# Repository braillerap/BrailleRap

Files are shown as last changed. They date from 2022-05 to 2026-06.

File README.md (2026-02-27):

<figure>
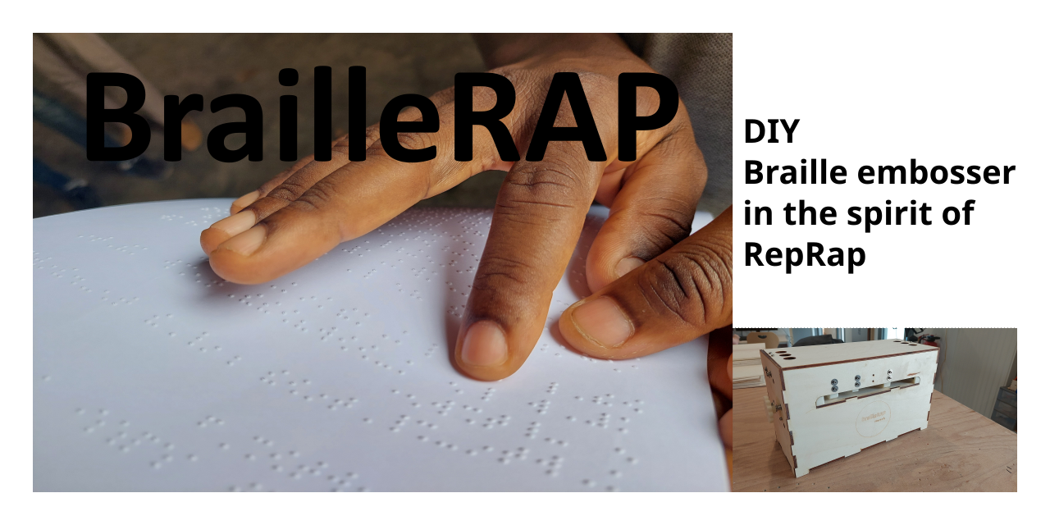
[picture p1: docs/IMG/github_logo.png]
BrailleRAP image

</figure>

# BrailleRAP

## Introduction
Based on a [RepRap 3d printer controller](https://reprap.org/wiki/RepRap), [BrailleRAP](https://github.com/braillerap/BrailleRap) is an open hardware device to emboss Braille text and/or Vector graphics. You can use software like [AccessBrailleRAP](https://github.com/braillerap/AccessBrailleRAP) or [DesktopBrailleRAP](https://github.com/braillerap/DesktopBrailleRAP) to translate text in Braille and build tangible documents with the device. Some tools like [OpenStreetTouch](https://github.com/braillerap/OpenStreetTouch) can help you extract data from [OpenStreetMap](https://www.openstreetmap.org) to build public transport guide or small area city map.

BrailleRAP now exist in 2 different sizes: **BrailleRAP** and **BrailleRAP XL**. 
- **BrailleRAP** emboss sheet up to 210x297 mm. Lightweight, a completed device will weight less than 5 kg and fit in cabin travel case. 
- **BrailleRAP XL** emboss sheet up to 297x420 mm. A larger surface if you need more space to emboss vector graphics. 

<figure>
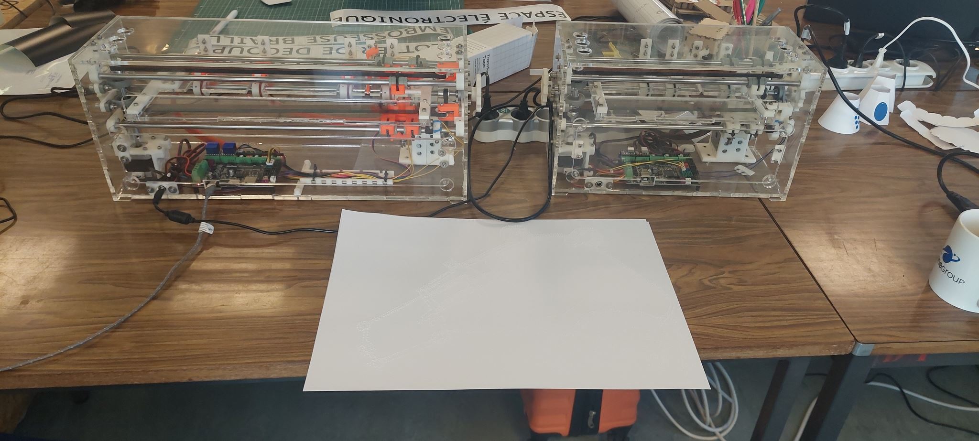
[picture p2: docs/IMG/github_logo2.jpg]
BrailleRAP and BrailleRAP XL image

</figure>

<figure>
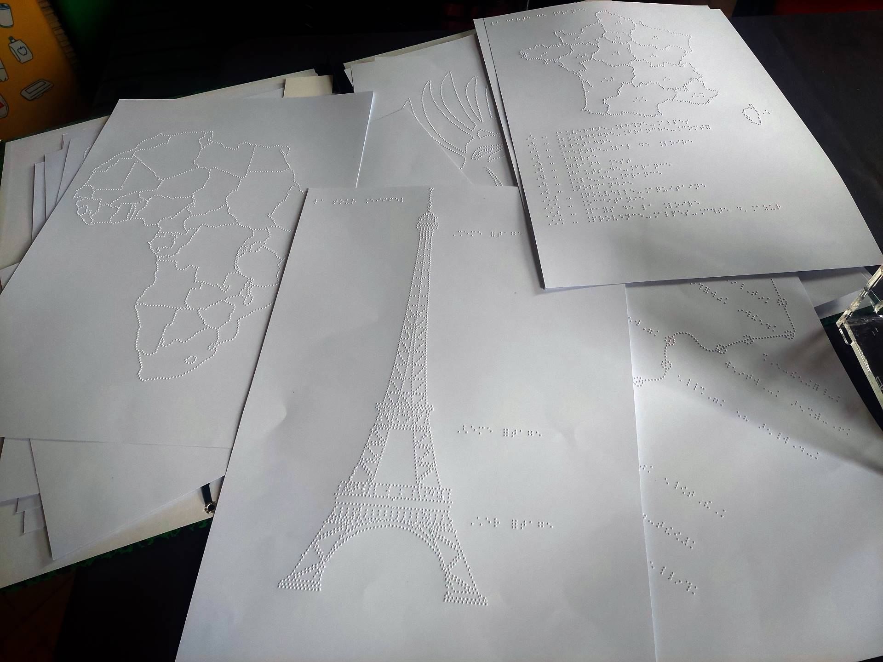
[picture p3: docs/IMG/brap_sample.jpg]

</figure>
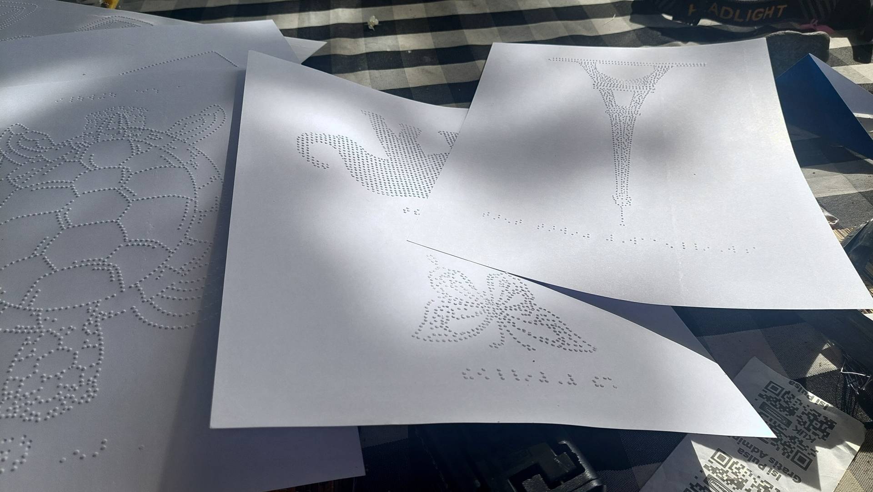
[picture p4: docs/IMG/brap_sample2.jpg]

</figure>

You may also find some interest in some 'side' projects to extend your BrailleRAP usage :

  [OpenStreetTangible](https://github.com/braillerap/OpenStreetTangible), a tangible subway map of the Rennes city in France. A custom build to demonstrate the ability of OpenStreetTouch and BrailleRAP to build accessible map.

  If you built a **BrailleRAP XL** maybe you want to carry it easily. The transport bag for the **BrailleRAP XL** is available [here](https://github.com/braillerap/braillerap-bag). Many thanks to [pasfou](https://github.com/pasfou) for this brilliant idea and realization.

  <figure>
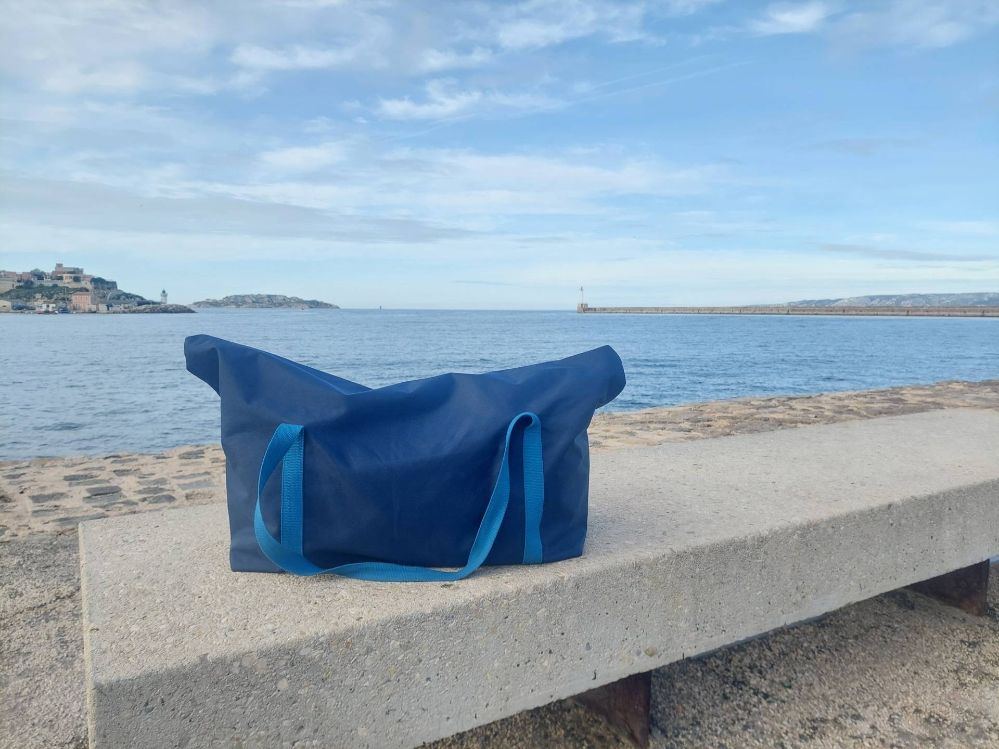
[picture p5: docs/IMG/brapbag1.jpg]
A custom bag for BrailleRAP XL
    
  </figure>

  **En_Bosse** a [Handitechlab Inria](https://project.inria.fr/handitechlabinria/fr/) project to process ultrasound imagery. The project AIM to emboss ultrasound imagery to make it available for visual impaired parents. [Em_Bosse](https://gitlab.inria.fr/handitechlabinria/enbosse/en_bosse/-/blob/main/README.md?ref_type=heads).

  **Carnet_de_sante** a [Handitechlab Inria](https://project.inria.fr/handitechlabinria/fr/) project to make children growing health data available for visual impaired peoples. [Carnet_de_sante](https://gitlab.inria.fr/handitechlabinria/enbosse/carnet_de_sante/-/blob/main/README.md?ref_type=heads).

  **Tactipix** a [Handitechlab Inria](https://project.inria.fr/handitechlabinria/fr/) starting collection of children illustrated books with audio resources (in french). The illustrations can be embossed on BrailleRAP. [Tactipix](https://handitechlabinria.gitlabpages.inria.fr/tactipix/)

## OSHWA Certification

BrailleRAP is [OSHWA](https:oshwa.org) open source hardware certified.
<a href="https://certification.oshwa.org/fr000027.html">
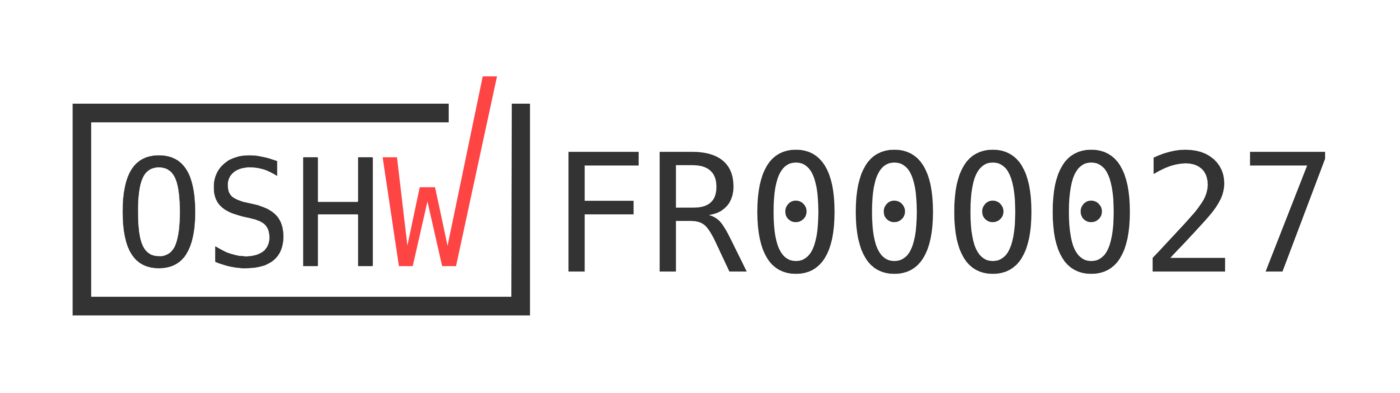
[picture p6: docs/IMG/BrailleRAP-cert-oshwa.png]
OSHWA certificate

</a>

## Building manual
The building manual translation files are available [on codeberg weblate host](https://translate.codeberg.org/projects/braillerap-building-manual/) . If you need the building manual in your language, feel free to contribute on codeberg/weblate.    

<a href="https://translate.codeberg.org/engage/braillerap-building-manual/">
User manual translation status
</a>

## Funding

This project is funded through [NGI0 Entrust](https://nlnet.nl/entrust), a fund established by [NLnet](https://nlnet.nl) with financial support from the European Commission's [Next Generation Internet](https://ngi.eu) program. Learn more at the [NLnet project page](https://nlnet.nl/project/BrailleRAP).

[NLnet foundation logo](https://nlnet.nl)
[NGI Zero Logo](https://nlnet.nl/entrust)

## BrailleRap 6.x Building Manual

Embosseuse Braille Open Source DIY



La documentation complete [est disponible ici braillerap.readthedocs.io](https://braillerap.readthedocs.io/fr/latest/index.html).

==========================================================================

DIY Open Source Braille embosser



The full documentation [is available at braillerap-en.readthedocs.io](https://braillerap-en.readthedocs.io/en/latest/index.html).

## Repository Structure

### `docs/`
The source file for readthedoc documentation, viewable at [braillerap.readthedocs.io](https://braillerap.readthedocs.io/fr/latest/index.html).

### `lasercut/`
SVG/DXF file for laser cut

### `MarlinBraille/`
BrailleRAP Firmware for MKS GEN 1.4 & MKS GEN L 2.1.

The firmware is already configured for DRV8825 stepper drivers.

### `printed_parts/`
STL files for 3D printed parts.

There is an xlsx (3D printed parts excel board.xlsx) files that detail the parts to print.

### `NatBrailleTools/`
Java source code for NatBraille BrailleRAP driver. This is obsolete now. Consider using AccessBrailleRAP (https://github.com/braillerap/AccessBrailleRAP) instead.

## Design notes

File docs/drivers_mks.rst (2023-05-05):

Windows USB Drivers pour MKS 1.4 ou MKS GEN L 2.1
=================================================

Pour MakerBase MKS 1.4
----------------------

Télécharger le driver FTDI (Virtual COM Port Drivers) ici: https://ftdichip.com/drivers/vcp-drivers/

Installer le driver

Pour MakerBase MKS GEN L 2.1
----------------------------

Télécharger le driver CH340 (CH341SER.EXE) ici : https://www.wch.cn/download/CH341SER_ZIP.html

Installer le driver

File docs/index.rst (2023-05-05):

Bienvenue sur la documentation BrailleRAP 
=========================================

.. image :: ./IMG/brailleRAP_couv.jpg 
  :width: 400px
  :align: center

|
 
Contenu:

.. toctree::
   :maxdepth: 1

   history
   licence
   bom
   assemblage
   drivers_mks
   marlin
   firstembossingpage

.. index:: history, licence, bom, marlin, assemblage, firstembossingpage

Mise à jour: |today|

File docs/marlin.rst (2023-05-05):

Marlin Firmware pour cartes Ramps ou compatibles
================================================

.. Note:: Le firmware Marlin est utilisé pour contrôler l'embosseuse Braille. Nous utilisons la configuration CNC pour contrôler l'électro-aimant avec les commandes associées au moteur de CNC / stylo / laser (GCODE M3 et M4)

.. Note:: Le firmware Marlin qui se trouve dans le repertoire MarlinBraille https://github.com/braillerap/BrailleRap/tree/master/MarlinBraille est déja configuré pour la BrailleRAP. Si vous n'avez pas effectué de modifications par rapport à la documentation, vous pouvez l'utiliser directement sans vous préoccuper de la configuration Marlin

Configuration Marlin
--------------------
 
in configuration.h

Motherboard configuration ::

   #ifndef MOTHERBOARD
     //#define MOTHERBOARD BOARD_RAMPS_14_EFB
     #define MOTHERBOARD BOARD_RAMPS_14_SF
   #endif

Spindle / laser / pen configuration ::

   // BRAILLE RAP CONFIG
   #define SPINDLE_LASER_ENABLE
   #define SPINDLE_LASER_ENABLE_PIN  RAMPS_D8_PIN      // !!! for BED MOSFET
   #define SPINDLE_LASER_PWM_PIN     RAMPS_D10_PIN     // !!! for E0 MOSFET
   #define SPINDLE_DIR_PIN           5                 // pin servo

Endstop configuration ::

   // Mechanical endstop with COM to ground and NC to Signal uses "false" here (most common setup).
   #define X_MIN_ENDSTOP_INVERTING false // set to true to invert the logic of the endstop.
   #define Y_MIN_ENDSTOP_INVERTING false // set to true to invert the logic of the endstop.
   #define Z_MIN_ENDSTOP_INVERTING false // set to true to invert the logic of the endstop.
   #define X_MAX_ENDSTOP_INVERTING false // set to true to invert the logic of the endstop.
   #define Y_MAX_ENDSTOP_INVERTING false // set to true to invert the logic of the endstop.
   #define Z_MAX_ENDSTOP_INVERTING false // set to true to invert the logic of the endstop.
   #define Z_MIN_PROBE_ENDSTOP_INVERTING false // set to true to invert the logic of the probe.

Motor step / mm ::

   #define DEFAULT_AXIS_STEPS_PER_UNIT   { 80, 46, 4000, 500 }

Max feedrate ::

   #define DEFAULT_MAX_FEEDRATE          { 300, 300, 5, 25 }

Acceleration ::

   #define DEFAULT_MAX_ACCELERATION      { 1500, 1500, 100, 10000 }

   #define DEFAULT_ACCELERATION          1500    // X, Y, Z and E acceleration for printing moves
   #define DEFAULT_RETRACT_ACCELERATION  1500    // E acceleration for retracts
   #define DEFAULT_TRAVEL_ACCELERATION   1500    // X, Y, Z acceleration for travel (non printing) moves

Jerk ::

   #define DEFAULT_XJERK                 5.0
   #define DEFAULT_YJERK                 5.0
   #define DEFAULT_ZJERK                 0.3
   #define DEFAULT_EJERK                 5.0

.. Note:: Dans la version présente sur le github du projet BrailleRap, d'autres fichiers ont été modifiés pour gérer l'alimentation du papier avec le fin de course de l'axe Y.

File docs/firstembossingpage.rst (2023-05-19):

Embosser votre première page de Braille
=======================================

BrailleRap est une machine qui se pilote en G-CODE, pour embosser du braille il faut tout d'abord traduire le texte en Braille.
Il existe 3 solutions pour traduire le Braille :
L'application AccessBrailleRap https://github.com/braillerap/AccessBrailleRAP/releases
L'application BrailleRap en ligne https://crocsg.github.io/BrailleRap/
L'application NatBraille http://natbraille.free.fr  

Utilisation de l'application AccessBrailleRap
---------------------------------------------
Utiliser le bouton "Paramêtres" pour accéder à l'écran de paramétrage

.. image :: ./IMG/AccBrap-3.png
    :align: center

Choisisser la table Braille de votre choix, le port de communication pour piloter BrailleRAP,
et la langue de l'application

|

Utiliser le bouton "Saisie" pour accéder à l'écran de saisie du texte
Entrer le texte de votre choix, vous pouvez utiliser le copier coller pour 
utiliser un texte existant (page web, document word ...)

.. image :: ./IMG/AccBrap-1.png
    :align: center

|

Utiliser le bouton "Impression" pour accéder à l'écran de d'impression
Sélectionner la page que vous souhaitez embosser avec les boutons "Page précédente" et "Page suivante".
Pour embosser le texte, installer une feuille de papier dans BrailleRAP et utiliser le bouton "Imprimer"

.. image :: ./IMG/AccBrap-2.png
    :align: center

|

Utilisation de l'application BrailleRap
---------------------------------------

Aller sur la page https://crocsg.github.io/BrailleRap/

.. image :: ./IMG/braillerapapp.png 
       :align: center
       
Entrer votre texte à l'endroit indiqué, et télécharger ensuite le fichier GCODE contenant les instructions pour l'embosseuse

.. image :: ./IMG/braillerapapp_download.png
       :align: center

Vous pouvez ensuite utiliser un logiciel comme **cura** ou **pronterface** pour envoyer le fichier GCODE à l'imprimante

Configuration NatBraille
------------------------

Compiler les programmes dans le repertoire NatBrailleTools du projet

Dans les options générales NatBraille, utiliser **TbFr2007** pour la table braille, Encodage document noir **Automtique**, Encodage document braille **Windows1252**

.. image :: ./IMG/natbraille.png
       :align: center

Dans les options d'embossage, utiliser **TbFr2007** pour la table braille pour l'embossage

Activer l'option **utiliser une commande systeme pour l'embossage**

le paramêtre  pour commande d'impression est : **java -jar d:\\usr\\home\\logger\\BrailleLogger.jar $f | java -jar d:\\usr\\home\\logger\\gcodestreamer.jar COM4 250000**
en modifiant eventuellement les repertoires d'installation des programmes
COM4 est le port serie utilisé pour communiquer avec l'imprimante

.. image :: ./IMG/natbrailleembossig.png
       :align: center

Dans les options de mise en page, indiquer 31 et 26 dans le nombre de caracter par ligne et le nombre de lignes par page

.. image :: ./IMG/natbraille_page.png
       :align: center

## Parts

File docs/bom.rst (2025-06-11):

Liste du matériel
=================

Découpe laser
-------------

Pour BrailleRAP
<<<<<<<<<<<<<<<
2 planches de contreplaqué 5mm en 600mm x 400mm.

Les fichiers au format dxf sont disponibles ici : https://github.com/BrailleRap/BrailleRap/tree/master/lasercut
   * lasercut/Braillerap_v6-5-1_600x400-planche1.svg
   * lasercut/Braillerap_v6-5-1-600x400-planche2.svg

Pour BrailleRAP XL
<<<<<<<<<<<<<<<<<<
2 planches de contreplaqué 5mm en 900mm x 400mm.

Les fichiers au format dxf sont disponibles ici : https://github.com/BrailleRap/BrailleRap/tree/master/lasercut
   * lasercut/brapxl-v6.6-planche1_900x400.svg
   * lasercut/brapxl-v6-6-planche2_900x400.svg

Pièces imprimées
----------------
Toutes les pièces sont imprimées en ABS, 50% de remplissage, 3 périmètres extérieurs. Nous utilisons le filament eSun ABS Natural.

Les fichiers au format stl sont ici : https://github.com/braillerap/BrailleRap/tree/master/printed_parts

Pièces mécaniques
-----------------

Pour BrailleRAP
<<<<<<<<<<<<<<<

=== =========================================
Qty Type
=== =========================================
4   Rail de guidage linéaire ( diamètre 8mm ) **330 mm** length
1   Rail de guidage linéaire ( diamètre 8mm ) **365 mm** length
1   Rail de guidage linéaire ( diamètre 8mm ) **100 mm** length

2   630 mm de courroie GT2

3   Joints torique 15.1 mm diamètre intérieur 20.5 mm de diamètre extérieur (15.1 x 20.5 x 2.7)
3   Ressorts tendeurs de courroie GT2

...
=== =========================================

Pour BrailleRAP XL
<<<<<<<<<<<<<<<<<<

=== =========================================
Qty Type
=== =========================================
4   Rail de guidage linéaire ( diamètre 8mm ) **470 mm** length
1   Rail de guidage linéaire ( diamètre 8mm ) **505 mm** length
1   Rail de guidage linéaire ( diamètre 8mm ) **100 mm** length

2   960 mm de courroie GT2

4   Joints torique 15.1 mm diamètre intérieur 20.5 mm de diamètre extérieur (15.1 x 20.5 x 2.7)
4   Ressorts tendeurs de courroie GT2
...
=== =========================================

Pièces communes BrailleRAP XL / BrailleRAP
<<<<<<<<<<<<<<<<<<<<<<<<<<<<<<<<<<<<<<<<<<

=== =========================================
Qty Type
=== =========================================
6   RJ4JP-01-08 palier linéaire Polymer  

3   GT2 poulie 20 dents pour axe 8mm    
2   GT2 poulie libre 20 dents axe 3mm (avec roulement à billes)
1   GT2 poulie 20 dents pour axe 5mm

2   KP08  pallier horizontal pour rail linéaire 8mm 
2   KFL08 pallier vertical pour rail linéaire 8mm 

1   Accouplement d'axe 5mm/8mm

1   Courroie GT2 fermée 200 mm

10	Colliers de serrage 2.5 x 160 mm

...
=== =========================================

Carte controleur
----------------
En fonction de vos souhaits vous pouvez utiliser au choix :

- Une carte MKS GEN 1.4 (Mega2560) et 2 drivers DRV8825 https://github.com/makerbase-mks
- Une carte MKS GEN-L (Mega2560) et 2 drivers DRV8825 https://github.com/makerbase-mks
- Une carte MKS TinyBee (ESP32) et 2 drivers TMC2209 https://github.com/makerbase-mks

D'autres configuration sont possibles, mais vous devrez effectuer la configuration du firmware vous même

Electronique
------------

=== ===========================================================================================
Qty Type
=== ===========================================================================================
2   Moteurs Nema 17 40 N/cm 40mm avec câble (17HS4401).        
1   Electro-aimant *tau-826b* 12V 2A.
1   MKS GEN 1.4 ou carte compatible Ramps 1.4 ou MKS GEN L 2.1 https://github.com/makerbase-mks.
2   drivers DRV8825 avec radiateur.
1   1N4004  diode de roue libre ou equivalent (12V 2A) (pour MKS GEN 1.4 uniquement).    
2   Commutateurs fin de course cablés conformément à la documentation. (OMRON `SS-5GL <https://omronfs.omron.com/en_US/ecb/products/pdf/en-ss.pdf>`_ ou compatible)
1   Embase Alimentation jack 2.5mm. 
1   Alimentation 12v 6A jack 2.5mm.

=== ===========================================================================================

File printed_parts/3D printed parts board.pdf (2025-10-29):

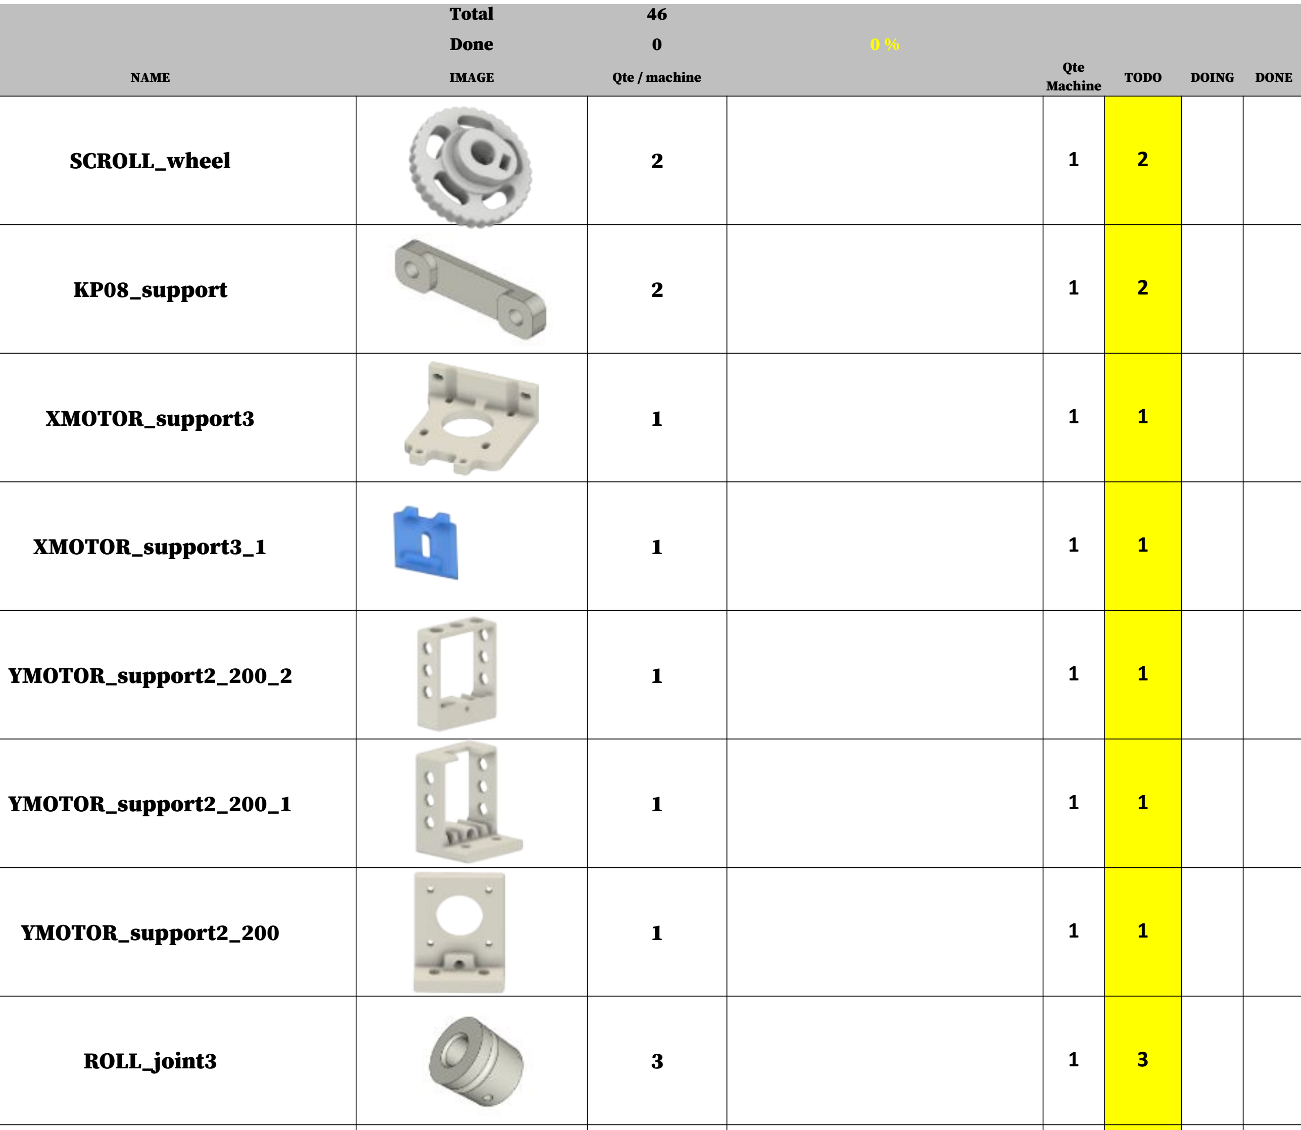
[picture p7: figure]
Total; Done; NAME; IMAGE; Qte / machine; TODO; DOING DONE; SCROLL_wheel; KP08_support; XMOTOR_support3; XMOTOR_support3_1; YMOTOR_support2_200_2; YMOTOR_support2_200_1; YMOTOR_support2_200; ROLL_joint3; Qte Machine
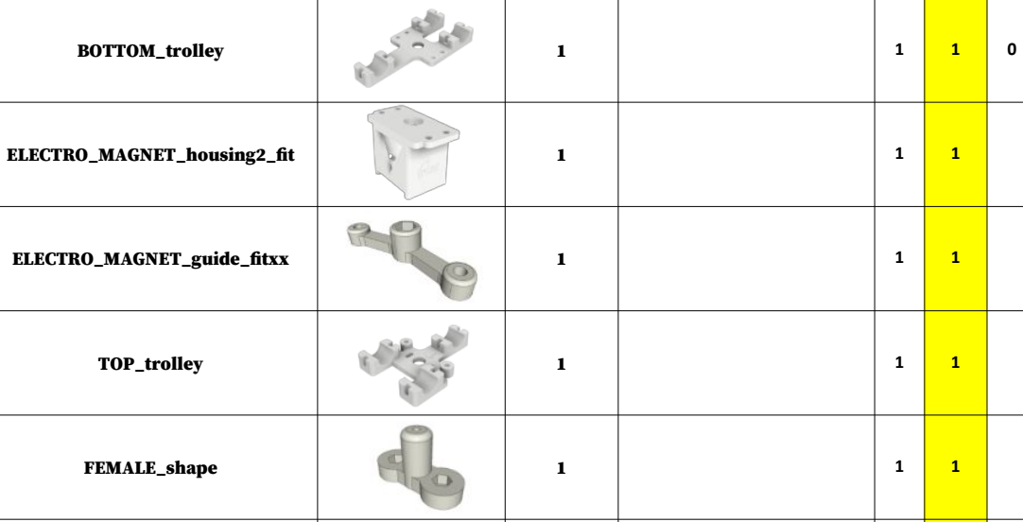
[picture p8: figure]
BOTTOM_trolley; ELECTRO_MAGNET_housing2_fit; ELECTRO_MAGNET_guide_fitxx; TOP_trolley; FEMALE_shape

LID_LOCK | 2 | 1 | 2
BOTTOM_AXIS_left2 | 1 | 1 | 1

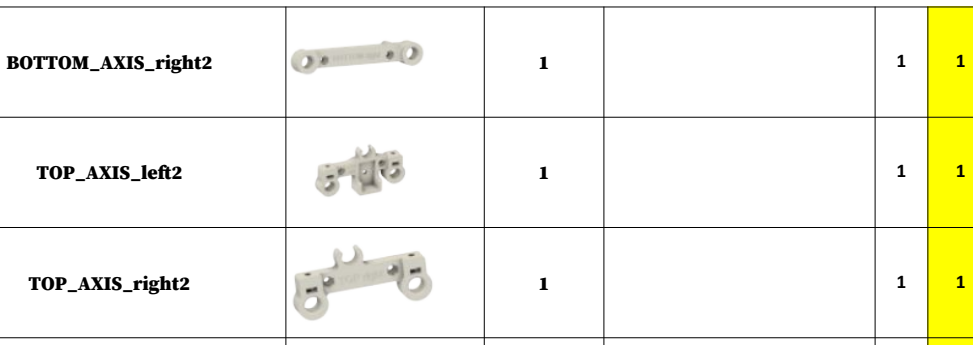
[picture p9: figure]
BOTTOM_AXIS_right2; TOP_AXIS_left2; TOP_AXIS_right2

DRIVEN_PULLEY_housing | 2 | 1 | 2
PAPER_GUIDE_left (A4) or paper_guide_left (XL) | 1 | 1 | 1
PAPER_GUIDE_right (A4) or paper_guide_right (XL) | 1 | 1 | 1
ENDSTOP_Y_support | 1 | 1 | 1
ENDSTOP_Y_lever_weight2 | 1 | 1 | 1
ENDSTOP_X_support | 1 | 1 | 1
CLIPBOARD_2 | 4 | 1 | 4
CLIPBOARD_2_SUPPORT | 4 | 1 | 4

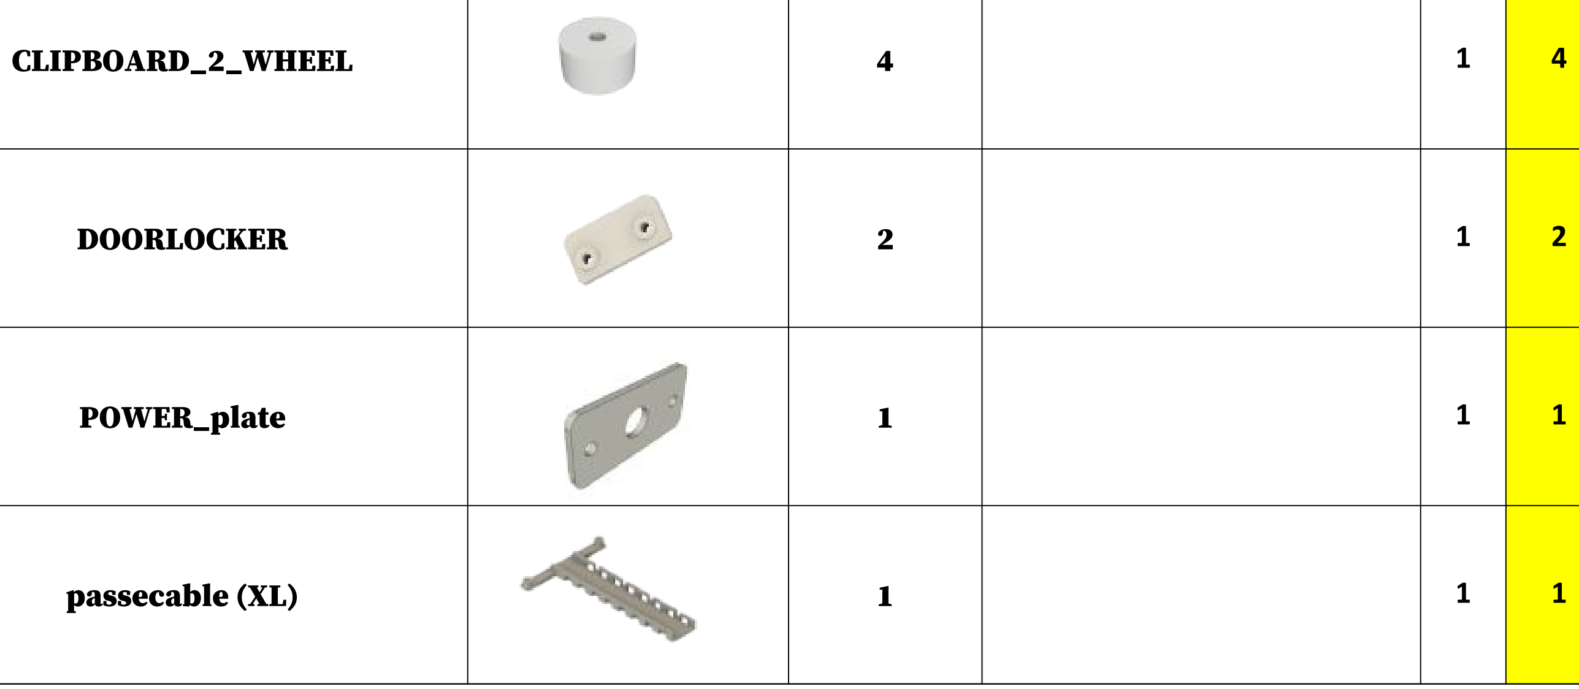
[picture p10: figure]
CLIPBOARD_2_WHEEL; DOORLOCKER; POWER_plate; passecable (XL)

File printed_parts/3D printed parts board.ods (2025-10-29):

 | Total | 46
 | Done | 0 | 0 %
NAME | IMAGE | Qte / machine |  | Qte Machine | TODO | DOING | DONE
SCROLL_wheel |  | 2 |  | 1 | 2
KP08_support | Capture d’écran 2018-04-30 à 12.50.34.png | 2 |  | 1 | 2
XMOTOR_support3 |  | 1 |  | 1 | 1
XMOTOR_support3_1 |  | 1 |  | 1 | 1
YMOTOR_support2_200_2 |  | 1 |  | 1 | 1
YMOTOR_support2_200_1 |  | 1 |  | 1 | 1
YMOTOR_support2_200 |  | 1 |  | 1 | 1
ROLL_joint3 | Capture d’écran 2018-04-23 à 12.45.35.png | 3 |  | 1 | 3
BOTTOM_trolley |  | 1 |  | 1 | 1 | 0
ELECTRO_MAGNET_housing2_fit |  | 1 |  | 1 | 1
ELECTRO_MAGNET_guide_fitxx | Capture d’écran 2018-04-30 à 13.00.29.png | 1 |  | 1 | 1
TOP_trolley |  | 1 |  | 1 | 1
FEMALE_shape | Capture d’écran 2018-04-23 à 13.38.51.png | 1 |  | 1 | 1
LID_LOCK | Capture d’écran 2018-04-23 à 13.41.41.png | 2 |  | 1 | 2
BOTTOM_AXIS_left2 |  | 1 |  | 1 | 1
BOTTOM_AXIS_right2 |  | 1 |  | 1 | 1
TOP_AXIS_left2 |  | 1 |  | 1 | 1
TOP_AXIS_right2 |  | 1 |  | 1 | 1
DRIVEN_PULLEY_housing | Capture d’écran 2018-04-26 à 10.52.19.png | 2 |  | 1 | 2
PAPER_GUIDE_left (A4) or paper_guide_left (XL) |  | 1 |  | 1 | 1
PAPER_GUIDE_right (A4) or paper_guide_right (XL) |  | 1 |  | 1 | 1
ENDSTOP_Y_support |  | 1 |  | 1 | 1
ENDSTOP_Y_lever_weight2 |  | 1 |  | 1 | 1
ENDSTOP_X_support |  | 1 |  | 1 | 1
CLIPBOARD_2 |  | 4 |  | 1 | 4
CLIPBOARD_2_SUPPORT |  | 4 |  | 1 | 4
CLIPBOARD_2_WHEEL |  | 4 |  | 1 | 4
DOORLOCKER |  | 2 |  | 1 | 2
POWER_plate | Capture d’écran 2018-06-03 à 10.23.29.png | 1 |  | 1 | 1
passecable (XL) |  | 1 |  | 1 | 1

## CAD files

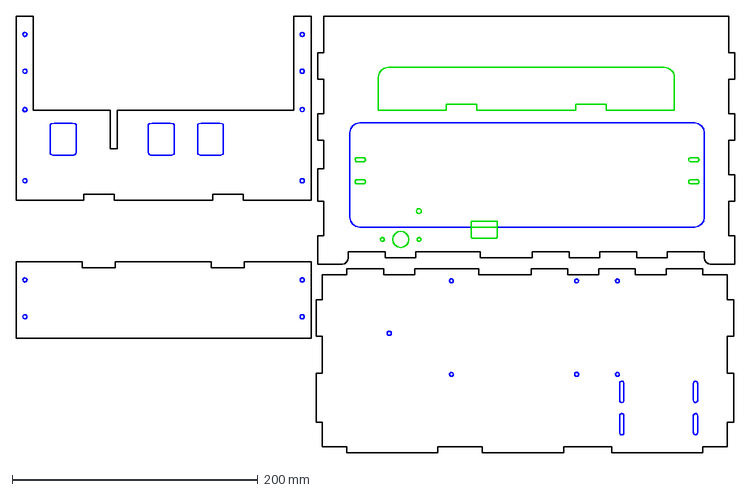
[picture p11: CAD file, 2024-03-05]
lasercut/Braillerap_v6-5-1-600x400-planche2.dxf
585.6 x 355.9 mm

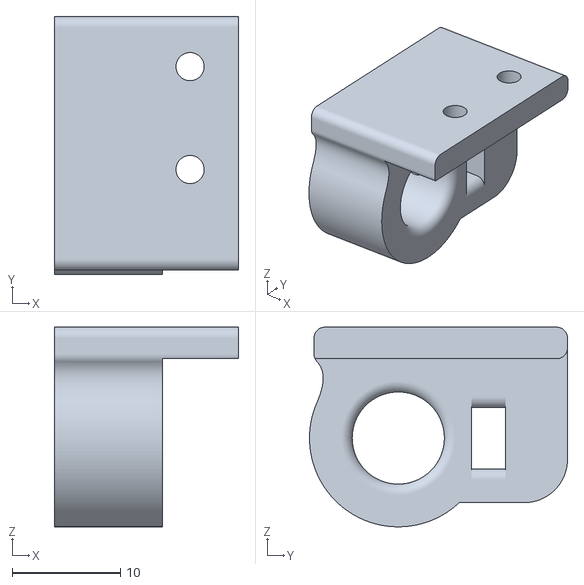
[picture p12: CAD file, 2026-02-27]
printed_parts/ENDSTOPX_support2.stl
17.0 x 23.8 x 18.4

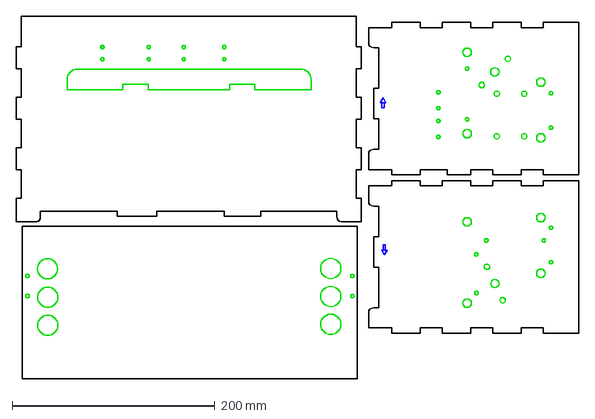
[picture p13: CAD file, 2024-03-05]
lasercut/Braillerap_v6-5-1_600x400-planche1.dxf
553.9 x 356.7 mm

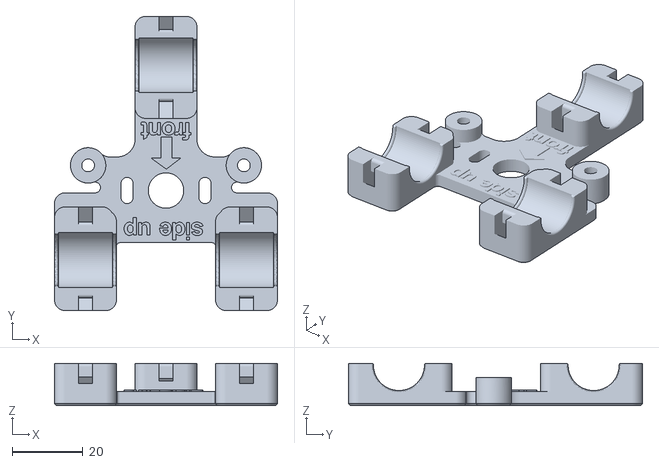
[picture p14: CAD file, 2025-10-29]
printed_parts/TOP_trolley.stl
63.0 x 83.1 x 12.0

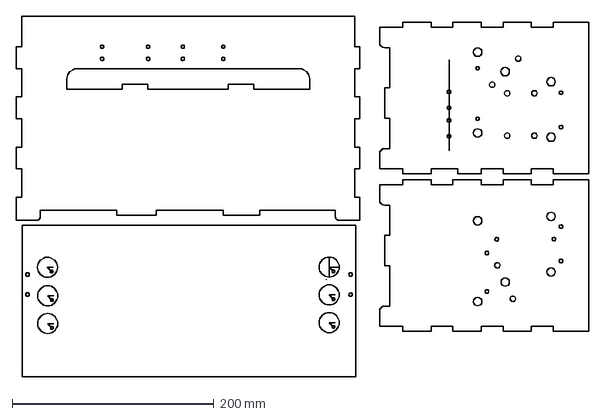
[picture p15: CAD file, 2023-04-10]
lasercut/BrailleRAP V6-5 600x400 planche1.dxf
566.6 x 356.7 mm

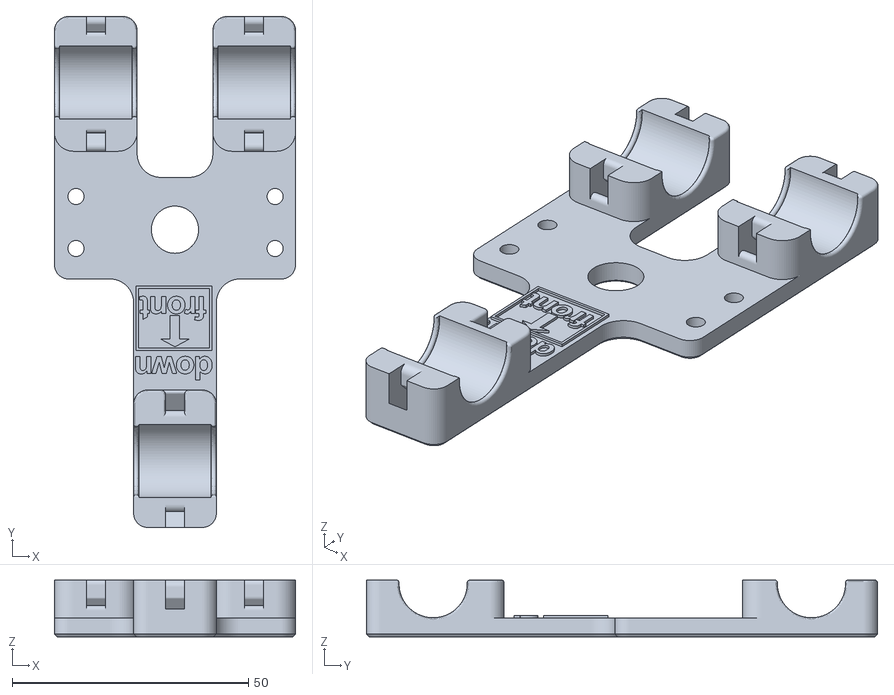
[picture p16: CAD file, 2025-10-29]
printed_parts/BOTTOM_trolley.stl
51.0 x 108.1 x 12.0

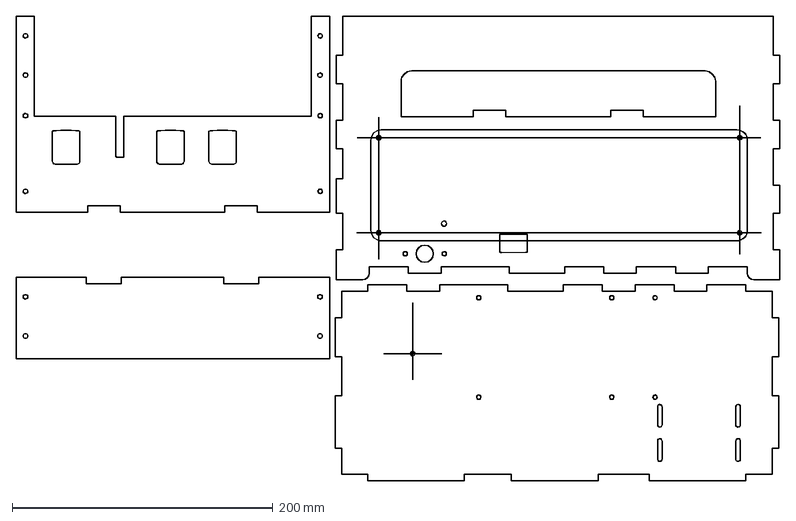
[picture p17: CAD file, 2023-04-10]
lasercut/BrailleRAP V6-5 600x400 planche2.dxf
585.6 x 355.9 mm

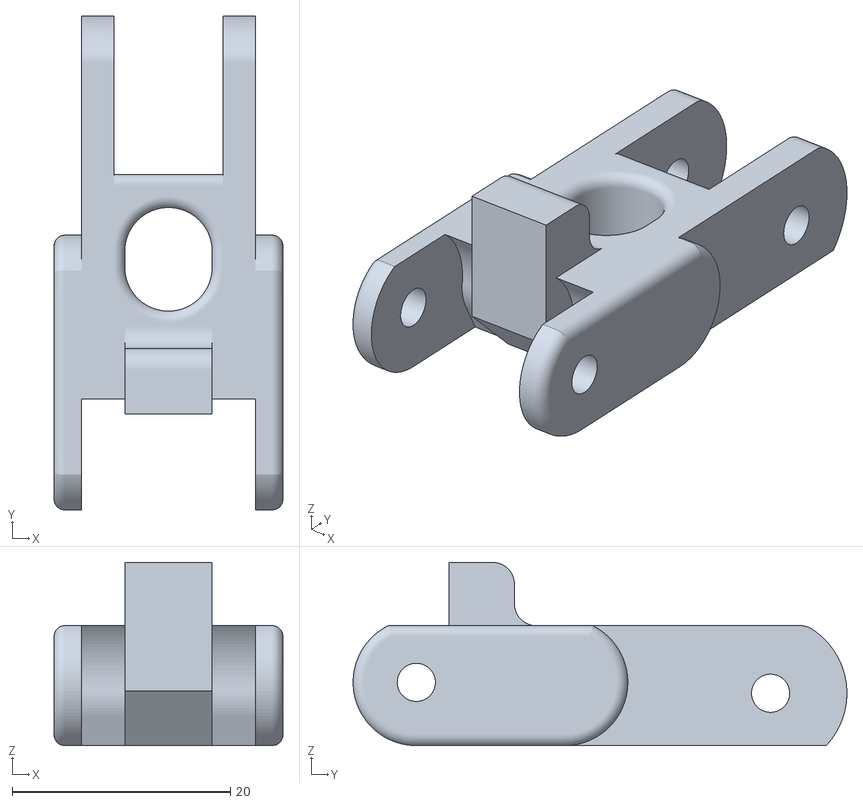
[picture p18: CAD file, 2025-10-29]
printed_parts/clipboard2.stl
21.0 x 45.3 x 16.8

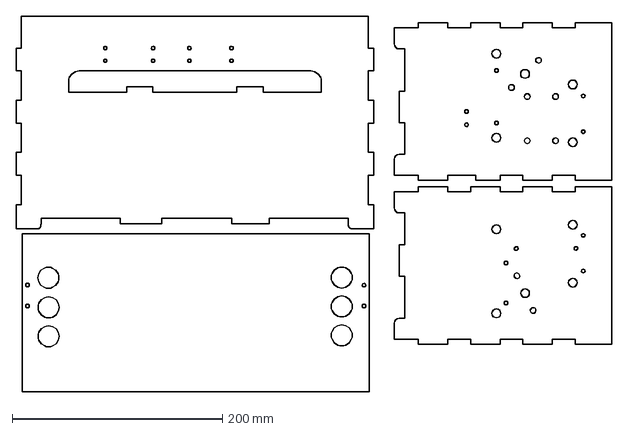
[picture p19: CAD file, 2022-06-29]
lasercut/BrailleRAP V6 600x400 planche1.dxf
566.6 x 356.7 mm

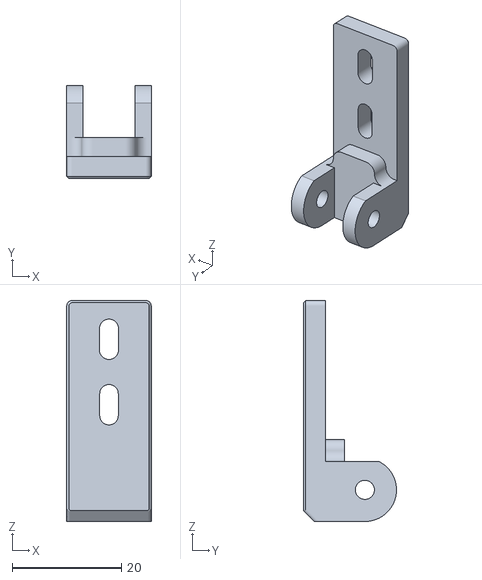
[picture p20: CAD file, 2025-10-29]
printed_parts/clipboard2_support.stl
15.5 x 17.0 x 40.5

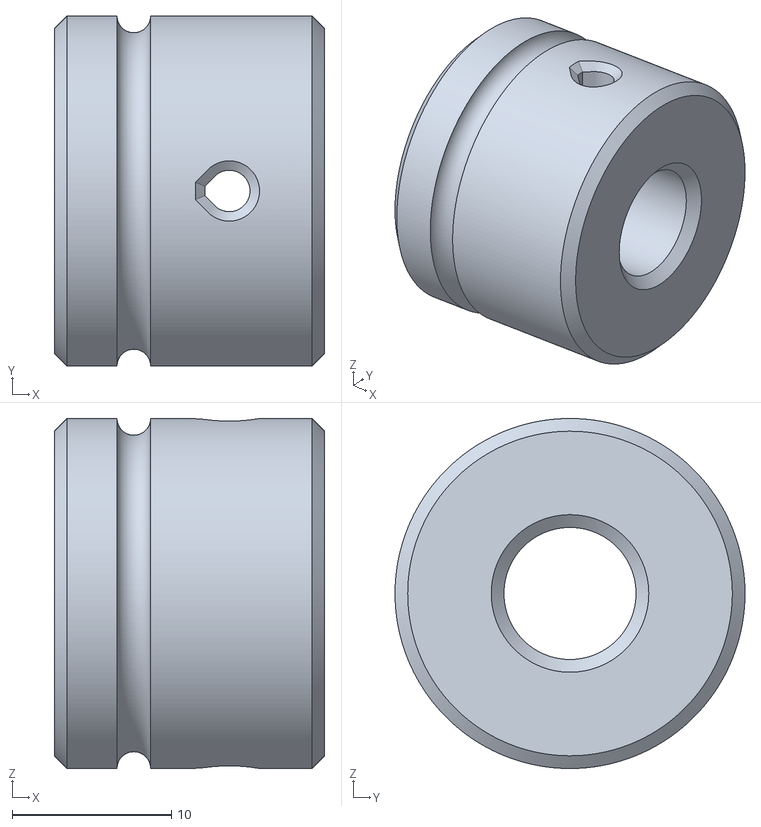
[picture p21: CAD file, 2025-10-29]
printed_parts/ROLL_JOINT3.stl
17.0 x 22.0 x 22.0

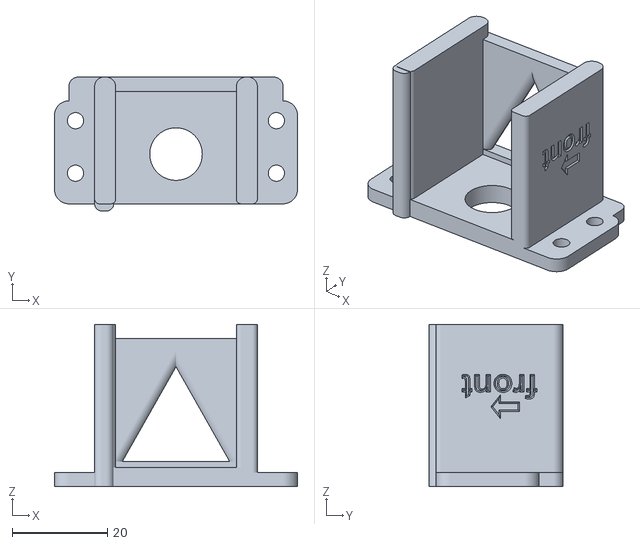
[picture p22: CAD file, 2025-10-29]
printed_parts/ELECTRO_MAGNET_housing_fit.stl
50.9 x 28.1 x 34.0

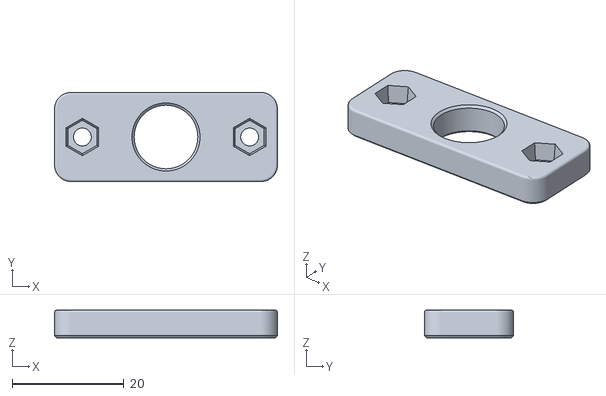
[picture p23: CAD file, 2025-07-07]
printed_parts/power_plate_10mm.stl
40.0 x 16.0 x 5.00

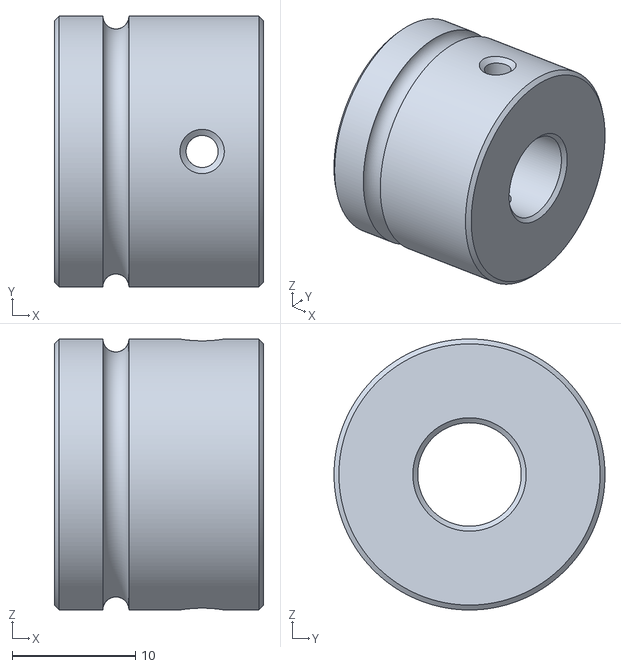
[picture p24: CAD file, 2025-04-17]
printed_parts/ROLL_JOINT2_test.stl
17.0 x 22.0 x 22.0

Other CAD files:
printed_parts/ROLL_JOINT2.stl
printed_parts/YMOTOR_support2_200.stl
printed_parts/YMOTOR_support2_200_1.stl
printed_parts/ELECTRO_MAGNET_housing2.stl
lasercut/BrailleRAP V5 600x400 planche1.dxf
lasercut/OLD/BrailleRAP V5 600x400 planche1.dxf
lasercut/OLD/BrailleRAP V5 600x400 planche2.dxf
lasercut/OLD/BrailleRAP V6 600x400 planche2.dxf
printed_parts/BOTTOM_AXIS_right2.stl
printed_parts/CLIPBOARD2_WHEEL.stl
printed_parts/CLIPBOARD_WHEEL.stl
printed_parts/DOORLOCKER.stl
printed_parts/DRIVEN_PULLEY_housing.stl
printed_parts/ELECTRO_MAGNET_guide.stl
printed_parts/ELECTRO_MAGNET_guide_fit.stl
printed_parts/ELECTRO_MAGNET_guide_fit_5.7.stl
printed_parts/ELECTRO_MAGNET_guide_fit_5.8.stl
printed_parts/ELECTRO_MAGNET_guide_fit_5.9.stl
printed_parts/ELECTRO_MAGNET_guide_fit_6.0.stl
printed_parts/ENDSTOPX_support.stl
printed_parts/ENDSTOP_Y_lever_weight.stl
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

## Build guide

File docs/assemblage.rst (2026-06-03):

Manuel de montage BrailleRAP
============================

Outillages necessaires
----------------------

       - Petites pinces.
       - Petite pince coupante.
       - Un taraud M3.
       - 1 foret de 8mm.
       - 1 foret de 3mm.
       - Clés 6 pans 1.5, 2, 2.5 et 4. 
       - Clés à tube 5.5 et 8.
       - Colle à bois. 
       - Scotch de peintre.

Remarques sur les vis
---------------------

M3 et M5 correspondent au diamètre en mm de la partie taraudée des vis
Le deuxieme nombre correspond à la longueur de la vis
Par exemple M3-12 designe une vis de 3mm de diamètre et de 12mm de longueur

**M5-18** correspond à une vis avec une tête hexagonale (5mm de diamètre 18mm de longueur)
	
	.. image :: ./IMG/vis6pans.jpg
		:align: center

|

**M3-12 sans tête** correspond a une vis sans tête (3mm de diamètre - 12 mm de longueur)

	.. image :: ./IMG/vissantete.jpg
		:align: center

|

Remarques sur les écrous
------------------------

**Ecrou M3 ou ecrou M5** désignent des ecrous standards de diamêtre 3mm ou 5mm

	.. image :: ./IMG/ecrou.jpg
		:align: center

|

**Ecrou M3 NYL** ou **ecrou M5 NYL** désignent des ecrous **frein** de diamêtre 3mm ou 5mm
	
	.. image :: ./IMG/ecrounyl.jpg
		:align: center

|

Remarques BrailleRAP / BrailleRAP XL
------------------------------------

Il existe désormais 2 modèles de BrailleRAP: **BrailleRAP** et **BrailleRAP XL**.

**BrailleRAP** est la version historique de la machine et peut utiliser des feuilles jusqu'au format **A4**.
       
       * Braillerap_v6-5-1_600x400-planche1.svg
       * Braillerap_v6-5-1_600x400-planche2.svg

**BrailleRAP XL** est la version agrandie et peut utiliser des feuilles jusqu'au format **A3**.
       
       * brapxl-v6-6-planche1_900x400.svg
       * brapxl-v6-6-planche2_900x400.svg

Le montage des 2 modèles est très semblable, les principales différences sont :

    * Le montage du plateau papier.
    * Le nombre de rouleaux presse papier.
    * les longeurs de barres lineaires et les longueurs de courroie.
    * BrailleRAP XL demande tout de même un peu plus de rigueur dans l'assemblage mécanique.

|

Collage de la caisse en bois
----------------------------
Matériel:

    * FACE (contre-plaqué de 5mm découpé au laser).
    * BACK (contre-plaqué de 5mm découpé au laser).
    * BOTTOM (contre-plaqué de 5mm découpé au laser).
    * LEFT_SIDE (contre-plaqué de 5mm découpé au laser).
    * RIGHT_SIDE (contre-plaqué de 5mm découpé au laser).
    * Colle à bois.
    * Scotch de peintre.

* Préparer les 5 éléments: FACE, BACK, LEFT_SIDE, RIGHT_SIDE et BOTTOM.

.. ATTENTION:: bien repérer la position des cotés (droit et gauche) et le fond. Utiliser les percages pour orienter les pièces comme sur la figure

.. image :: ./IMG/gluing_chassis.png
       :align: center

|

* Encoller les encoches, assembler les 5 parties et les maintenir en place avec du scotch de peintre le temps du séchage préconisé par le fabricant.

.. image :: ./IMG/BrailleRAP-V5.01.jpg
       :align: center

|

Collage des bloqueurs de trappe
-------------------------------
Matériel:

    * Chassis assemblée.
    * 4 disques en bois récupérés de la découpe laser du couvercle.
    * Colle à bois.

* Coller les 4 disques de bois sur la façade arrière à l'intérieur de la caisse. Ces disques maintiendront la trappe d'accès à l'intérieur de la machine.

.. image :: ./IMG/chassis_disc.png
       :align: center

|

Collage du plateau papier
-------------------------------
Matériel:
	* Support papier supérieur.
	* Support papier inférieur.
	* Colle à bois.
	* Pinces de serrage.
	
.. image :: ./IMG/paper_support_parts.jpg
       :align: center

|

* Coller le support inférieur sous le support supérieur. 

.. image :: ./IMG/paper_support_v8.png
       :align: center

|

.. ATTENTION:: les 2 pièces doivent êtrent parfaitement alignées. Placer des vis dans les percages pour bien aligner les pièces. Il ne doit pas y avoir d'espace entre les deux pièces (ou la feuille de papier pourrait venir se coincer). Bien serrer les pièces l'une contre l'autre avec des pinces de serrages 

Préparation du pointeau Braille
-------------------------------

Matériel :

    * 1 Pierre à aiguisé
    * 1 vis sans tête M3-16 bout téton

* Limer l'arête du téton afin d’obtenir un profil approchant celui illustré.

.. image :: ./IMG/BrailleRAP-V5.56.jpg
       :align: center

|

Préparation Moteur X
--------------------
Matériel :

    * **Pièce(s) imprimée(s) en 3D** :  XMOTOR_support3 ou XMOTOR_support3_1 
    * 1 moteur Nema 17
    * 4 vis M3-8 
    * 2 écrous NYL M3
    * 2 vis M3-14
    
* Insérer 2 écrous NYL M3 dans la piece imprimée **XMOTOR_support3_1**.

.. image :: ./IMG/xmotor_support_assembly_v2_1.png
       :align: center

|

* Fixer les deux pièces imprimée **XMOTOR_support3_1** et **XMOTOR_support3** avec deux vis M3-14.

.. image :: ./IMG/xmotor_support_assembly_v1_2.png
       :align: center

|

* Fixer le moteur dans son support avec 4 vis M3-8. Ne pas serrer les vis, le moteur doit conserver un peu de jeu, il sera fixé ultérieurement.

.. image :: ./IMG/xmotor_support_assembly_v1_3.png
       :align: center

|

.. NOTE:: Attention à l'orientation du connecteur du moteur !

Préparation Moteur Y
--------------------

Matériel :

    * **Pièce(s) imprimée(s) en 3D** :  YMOTOR_support2_200_1, YMOTOR_support2_200_2, YMOTOR_support2_200
    * 1 moteur Nema 17
    * 1 poulie GT2 20 dents bore 5mm
    * 4 vis M3-8 
    * 2 vis M3-12

* Serrer la poulie sur l’arbre du moteur en s’assurant qu’au moins une des deux vis soit en face du méplat de l’axe du moteur et que les dents de la poulie soient orientées vers le moteur.

.. image :: ./IMG/BrailleRAP-V5.03.jpg
       :align: center

|

* Tarauder les deux cotés de la pièce centrale du support (**YMOTOR_support2_200_2**)

.. image :: ./IMG/ymotor_support_assembly_1.png
       :align: center
.. image :: ./IMG/ymotor_support_assembly_2.png
       :align: center

|

* Fixer les pieces **YMOTOR_support2_200_2** et **YMOTOR_support2_200_1** avec une Vis M3-12.

.. image :: ./IMG/ymotor_support_assembly3.png
       :align: center

|

* Fixer la piece **YMOTOR_support2_200** sur l'ensemble précédent avec une vis M3-12.

.. image :: ./IMG/ymotor_support_assembly_4.png
       :align: center

|

* Monter le moteur sur son support avec les 4 vis M3-8 en s'assurant que le connecteur du moteur soit dans la position correspondante à l'illustration.

.. image :: ./IMG/ymotor_support_assembly_5.png
       :align: center

|

* Introduire les écrous 4 NYL M3 dans le support moteur. Les maintenir en place avec un petit bout de scotch de peintre.

.. image :: ./IMG/ymotor_support_assembly_6.png
       :align: center

|

Préparation des supports d’axes
--------------------------------

  * **Pièce(s) imprimée(s) en 3D** : BOTTOM_AXIS_left2
  * **Pièce(s) imprimée(s) en 3D** : TOP_AXIS_left2
  * **Pièce(s) imprimée(s) en 3D** : TOP_AXIS_right2
  * 1 foret de 8mm
  * 6 écrous M3
  * 6 vis M3-12 sans tête

.. ATTENTION:: Selon la qualité d’impression des pièces en plastique, veiller à ce que les barres de 8mm puissent coulisser facilement dans leurs logements. Le cas échéant, percer le trou avec un foret de 8.

* Les 3 pièces à assembler sont les suivantes 

.. image :: ./IMG/Axis_assembly_v1.png
       :align: center

|

* Pour chacune des 3 pièces, introduire un écrou M3 dans les trous rectangulaires. Visser les vis M3-12.

.. image :: ./IMG/BrailleRAP-V5.09.1.jpg
       :align: center

|

* L’extrémité de la vis ne doit pas dépasser dans le passage des barres de Ø 8mm.

.. image :: ./IMG/BrailleRAP-V5.10.jpg
       :align: center

|

.. image :: ./IMG/BrailleRAP-V5.11.jpg
       :align: center

|

Préparation de l'interrupteur de fin de course X
------------------------------------------------

Matériel :

  * **Pièce(s) imprimée(s) en 3D** : SWITCH_X_support
  * 1 interrupteur fin de course câblé (cf câblage des interrupteurs fin de course)
  * 1 vis sans tête M3-12
  * 1 écrou M3
  * 2 vis M2.5-14
  * 2 écrous M2.5 NYL

* Introduire un écrou M3 et visser une vis sans tête M3-12.

.. image :: ./IMG/BrailleRAP-V5.45.png
       :align: center
.. image :: ./IMG/BrailleRAP-V5.45-1.png
       :align: center

|

* Visser l'interrupteur fin de course sur son support (ENDSTOP_X_support) à l'aide des vis M2.5-14 et des écrous M2.5.

.. Note:: L'interrupteur fin de course devra être câblé avant le montage.
.. Note:: Attention au sens des vis 2.5. La tête de la vis doit être sous le microswitch pour permettre le passage de l'axe linéaire.

.. image :: ./IMG/endtsopx_assembly.png
       :align: center

.. Note:: On utilisera de préférence un microswitch cablé dans l'alignement.

.. image :: ./IMG/endstop_droit.jpg
       :align: center

|

Préparation de l’électro-aimant
--------------------------------

Matériel :

  * 1 électro-aimant
  * 1 entretoise de 18mm
  * 1 vis sans tête M3-16 pointeau limée (cf Préparation du pointeau mâle)
  * 1 écrou M3
  * 1 rondelle M3 

* Visser l’entretoise à fond sur l’électro-aimant.

.. image :: ./IMG/BrailleRAP-V5.16.png
       :align: center

|

* Visser la vis M3-16 pointeau limée en la laissant dépasser de ± 6mm de l’entretoise.

.. image :: ./IMG/BrailleRAP-V5.17.png
       :align: center

|

Montage de l'electro-aimant sur son support
-------------------------------------------

Matériel :
  * Ensemble électro-aimant pré assemblé (cf Préparation de l électro-aimant)
  * **Pièce(s) imprimée(s) en 3D ** : ELECTRO_MAGNET_housing2 ou ELECTRO_MAGNET_Housing2_fit
  * 2 vis M3-8
  * 2 rondelles M3

* Sélectionner la pièce **ELECTRO_MAGNET_housing2** ou **ELECTRO_MAGNET_Housing2_fit**. Sur une imprimante 3D d'ancienne génération, on utilisera plutot **ELECTRO_MAGNET_housing2**. Sur une imprimante récente et ultra précise, on utilisera plutôt **ELECTRO_MAGNET_Housing2_fit**. Ce sont les même pièces, mais les tolérances mécaniques sont plus faible sur la version **fit**, ce qui permet un meilleur centrage de l'electro-aimant.

* Fixer l’électro-aimant sur son support avec les 2 vis M3-8 et 2 rondelles M3.

.. ATTENTION:: Respecter le côté de sortie des fils c'est important.

.. image :: ./IMG/BrailleRAP-V5.19.png
       :align: center

|

.. NOTE:: Veuiller à aligner soigneusement le bord du support et le bord de l'electro-aimant

.. image :: ./IMG/BrailleRAP-V5.19-1.png
       :align: center

|

Préparation du chariot bas (étape 1)
------------------------------------

Matériel :

  * Electro-aimant assemblé dans son support
  * **Pièce(s) imprimée(s) en 3D** : BOTTOM_trolley
  * **Pièce(s) imprimée(s) en 3D** : ELECTRO_MAGNET_guide_fitxxx
  * 3 paliers lineaires IGUS
  * 3 colliers de serrage 2.5 x 160
  * 4 écrous M3 NYL
  * 2 vis M3-16
  * 2 vis M3-20

.. NOTE:: Sélectionner la meilleure pièce ELECTRO_MAGNET_guide_fit_5.8 / ELECTRO_MAGNET_guide_fit_5.9 / ELECTRO_MAGNET_guide_fit_6.0. l'entretoise de l'éléctroaimant doit circuler librement avec le minimum de jeu mécanique.

* Introduire les 3 IGUS sur le support BOTTOM_trolley. Les fixer avec des colliers de serrage

.. ATTENTION:: Bloquer les IGUS dans le rainurage. Ne pas serrer les colliers trop fort, ils seront ajustés quand le chariot sera en place sur les rails linéaires

.. image :: ./IMG/bottom_trolley_ok_v9.png
       :align: center

.. image :: ./IMG/bottom_trolley_assembly_v1-1.png
       :align: center

|

.. ATTENTION:: Respecter la position du collier. Le verrouillage du collier doit être du coté de l'IGUS et vers la paroi de la machine.

.. image :: ./IMG/bottom_trolley_assembly-v4.png
       :align: center

|

* Assembler l'électro-aimant (préalablement monté dans son logement) sous le BOTTOM_trolley et le ELECTRO_MAGNET_guide avec les deux vis M3-16 et 2 écrous M3 NYL.

.. ATTENTION:: Selon la qualité de l'impression, il sera peut-être nécessaire de limer le logement de l'entretoise. Notez également que le corps de l'electro-aimant doit être le plus perpendiculaire possible à la plaque support (l'axe doit être au milieu du percage qui permet son pasage). 

.. ATTENTION:: Notez que les fils de l'electro-aimant doivent sortir du coté ou il y a un seul pallier IGUS.

.. image :: ./IMG/BrailleRAP-V5.14-3.png
       :align: center

|

* Visser les deux vis M3-20 (qui retiendront la courroie) et 2 écrous M3 NYL avec la tête de vis en dessous.

.. image :: ./IMG/BrailleRAP-V5.14-4.png
       :align: center

|

* Mettre une rondelle et serrer le contre écrou M3 en veillant à ce que la vis pointeau ne se visse pas en même temps dans l’entretoise. La rondelle empêche le contre écrou de se coincer dans le guide de l’entretoise.

.. image :: ./IMG/BrailleRAP-V5.14-5.png
       :align: center

.. image :: ./IMG/BrailleRAP-V5.18.png
       :align: center

|

.. NOTE:: L'axe de l'electroaimant doit pouvoir monter et descendre librement sans effort.

|

Preparation du chariot haut (étape 1)
-------------------------------------

Matériel :

  * **Pièce(s) imprimée(s) en 3D** : TOP_trolley
  * **Pièce(s) imprimée(s) en 3D** : FEMALE_shape
  * Taraud M3
  * 1 vis sans tête M3-30
  * 1 écrou borgne M3
  * 1 écrou M3
  * 2 vis M3-12
  * 2 rondelles M3
  * 2 vis M3-20
  * 4 écrous M3 NYL
  * 3 paliers lineaires IGUS
  * 3 colliers de serrage 2.5 x 160

* Encoller le pas de vis de l'écrou borgne et visser la vis M3-30 sans tête du côté **SANS** empreinte allen.

.. image :: ./IMG/BrailleRAP-V5.79.jpg
       :align: center

|

* Placer un contre écrou contre l'écrou borgne

* Tarauder la FEMALE_shape au 2/3 en partant du haut.

.. image :: ./IMG/BrailleRAP-V5.80.jpg
       :align: center

|

* Visser l’ensemble vis M3-30/écrou borgne pour le laisser dépasser ± 0,5mm.

.. image :: ./IMG/BrailleRAP-V5.81.jpg
       :align: center

|

* Assembler la FEMALE_shape sur le TOP_trolley avec les vis M3-12, les rondelles M3 et les écrous M3 NYL en laissant du jeu.

.. image :: ./IMG/BrailleRAP-V5.82.png
       :align: center

.. image :: ./IMG/BrailleRAP-V5.83.png
       :align: center

|

* Positionner les paliers IGUS sur la piece TOP_trolley.

.. image :: ./IMG/toptroley_assembly_empty_v3.png
       :align: center

.. image :: ./IMG/toptroley_assembly_norizlan_v3.png
       :align: center

|

* attacher les palliers IGUS avec des colliers de Fixation

.. NOTE:: Attention au sens des colliers. La fixation du collier doit être vers les parois de la machine.
.. NOTE:: Bloquer les IGUS dans le rainurage. Ne pas serrer les colliers trop fort, ils seront ajustés quand le chariot sera en place sur les rails linéaires

.. image :: ./IMG/toptroley_assembly_v3.png
       :align: center

* Monter les vis M3-20 et les écrous M3-NYL.

.. image :: ./IMG/BrailleRAP-V5.86.png
       :align: center

.. image :: ./IMG/BrailleRAP-V5.87.png
       :align: center

Préparation des rouleaux papier
-------------------------------
Matériel **BrailleRAP**:

  * **Pièce(s) imprimée(s) en 3D** : 3 x ROLL_joint3
  * 1 taraud M3
  * 3 joints toriques
  * 6 vis M3-6 sans tête 

Matériel **BrailleRAP XL**:

  * **Pièce(s) imprimée(s) en 3D** : 4 x ROLL_joint3
  * 1 taraud M3
  * 4 joints toriques
  * 8 vis M3-6 sans tête 
  
  * Tarauder les 3 ou 4 ROLL_joint3.

.. image :: ./IMG/BrailleRAP-V5.41.jpg
       :align: center

* Mettre les joints toriques dans la gorge des 3 ou 4 ROLL_joint3.

.. image :: ./IMG/BrailleRAP-V5.42.jpg
       :align: center

* Visser les vis M3-6 sans tête en s'assurant qu'elles ne dépassent pas à l'intérieur du trou. Vous devez pouvoir faire coulisser le rouleau sur un axe de 8 mm.

.. image :: ./IMG/BrailleRAP-V5.43.jpg
       :align: center

Préparation des presse-papiers (étape 1) :
------------------------------------------
Matériel **BrailleRAP**:

  * **Pièce(s) imprimée(s) en 3D** : 3 x **clipboard2_support**  3 x **clipboard2** 3 x **CLIPBOARD2_WHEEL**
  * 3 vis M3-25
  * 3 vis M3-20
  * 3 ressorts tendeurs de courroie GT2
  * 6 ecrous M3-NYL

Matériel **BrailleRAP XL**:

  * **Pièce(s) imprimée(s) en 3D** : 4 x **clipboard2_support**  4 x **clipboard2** 4 x **CLIPBOARD2_WHEEL**
  * 4 vis M3-25
  * 4 vis M3-20
  * 4 ressorts tendeurs de courroie GT2
  * 8 ecrous M3-NYL

  * Positionner le presse papier **clipboard2** par rapport au support **clipboard2_support**.

  .. image :: ./IMG/BrailleRAP-V6.113.png
       :align: center

|

  * Positionner le ressort entre **clipboard2** et **clipboard2_support**.  

  .. image :: ./IMG/BrailleRAP-V6.113.1.png
       :align: center
  
|

  * Assembler le ressort avec **clipboard2** et **clipboard2_support** avec une vis M3-25 et un écrou M3-NYL.       

  .. NOTE:: Ne pas serrer l'écrou M3-NYL **clipboard2** et **clipboard2_support** doivent pouvoir bouger librement.
  .. image :: ./IMG/BrailleRAP-V6.113.2.png
       :align: center

| 

  * Assembler le rouleau avec **CLIPBOARD2_WHEEL** avec **clipboard2** à l'aide une vis M3-20 et d'un écrou M3-NYL. 

  .. NOTE:: Ne pas serrer l'écrou M3-NYL **CLIPBOARD2_WHEEL** doit pouvoir tourner librement.      
  .. image :: ./IMG/BrailleRAP-V6.113.3.png
       :align: center

|

Préparation de l’axe vertical (étape 1)
---------------------------------------

Matériel :

  * **Pièces** : ensemble XMOTOR_support3, XMOTOR_support3_1 et Moteur
  * 2 vis M3-20
  * 2 écrous M3 NYL
  * 2 rondelles M3 larges

* Introduire les 2 vis et les 2 rondelles par l'exterieur. Et attacher le support avec 3 ecrou NYL sans serrer. 

.. Note:: Le jeu permettra ensuite d'aligner l'arbre du moteur avec l'axe vertical.

.. image :: ./IMG/motorx_mount_1.jpg
       :align: center

.. image :: ./IMG/motorx_mount_2.jpg
       :align: center

|

Fixation Moteur Y :
-------------------

Matériel :
    
    * le moteur Nema 17 monté sur la pièce **YMOTOR_support2_200** + **YMOTOR_support2_200_1** + **YMOTOR_support2_200_2**
    * 4 vis M3-14
    * 4 rondelles M3 larges

* Introduire les vis et les rondelles par l’extérieur et visser le support sur la caisse afin qu’il puisse encore coulisser dans les trous oblongs.

.. image :: ./IMG/ymotor_support_assembly_8.jpg
       :align: center

.. image :: ./IMG/ymotor_support_assembly_7.jpg
       :align: center

|

Fixation des supports GAUCHES des axes 
--------------------------------------

Matériel :

  * **Pièce(s) imprimée(s) en 3D** :  BOTTOM_AXIS_left2 préparé avec écrou et vis sans tête (cf Préparation de supports d’axes)
  * **Pièce(s) imprimée(s) en 3D** :  TOP_AXIS_left2 préparé avec écrou et vis sans tête (cf Préparation de supports d’axes)

  * 4 vis M3-14
  * 4 rondelles M3 larges
  * 4 écrous NYL M3

* Fixer les supports d’axe sur la caisse le BOTTOM_AXIS_left2 et TOP_AXIS_left2 à gauche en laissant un peu de jeu (vis+rondelle à l'extérieur et écrou à l'intérieur). Les vis seront serrées quand l'ensemble sera en place.

.. image :: ./IMG/BrailleRAP-V5.12.1.jpg
       :align: center

.. image :: ./IMG/BrailleRAP-V5.12.2.jpg
       :align: center

Fixation des supports DROITS des axes
-------------------------------------

Matériel :

  * **Pièce(s) imprimée(s) en 3D** :  BOTTOM_AXIS_right2
  * **Pièce(s) imprimée(s) en 3D** :  TOP_AXIS_right2 préparé avec écrou et vis sans tête (cf Préparation de supports d’axes)
  * 4 vis M3-14
  * 4 rondelles M3 larges
  * 4 écrous NYL M3

* Fixer les supports d’axe sur la caisse le BOTTOM_AXIS_right2 (attention à la position du repère) et TOP_AXIS_right2 à droite en laissant un peu de jeu (vis+rondelle à l'extérieur et écrou à l'intérieur). Les vis seront serrées quand l'ensemble sera en place.

.. image :: ./IMG/BrailleRAP-V5.12.3.jpg
       :align: center

.. image :: ./IMG/BrailleRAP-V5.12.4.jpg
       :align: center

Fixation des tendeurs de courroie
---------------------------------

Matériel :

  * **Pièce(s) imprimée(s) en 3D** :  2 x DRIVEN_PULLEY_housing
  * 2 vis M3-20
  * 2 rondelles M3 larges
  * 2 écrous NYL M3

* Insérer un écrou M3 NYL dans son logement et fixer les DRIVEN_PULLEY_housing avec une vis M3-20 et une rondelle.

.. image :: ./IMG/BrailleRAP-V5.44.jpg
       :align: center

.. image :: ./IMG/BrailleRAP-V5.13.3.jpg
       :align: center

.. image :: ./IMG/BrailleRAP-V5.13.5.jpg
       :align: center

* Laisser un jeu de ±5mm.

.. image :: ./IMG/BrailleRAP-V5.13.4.jpg
       :align: center

Assemblage des poulies libres de renvoi
---------------------------------------

Matériel :

  * 2 poulies libres 20 dents bore 3mm
  * 2 vis M3-25
  * 2 écrous NYL M3

* Commencer par insérer la poulie puis la vis M3-25. Visser avec un écrou M3 NYL sans trop serrer.

.. image :: ./IMG/BrailleRAP-V5.13.6.jpg
       :align: center

Montage du chariot bas (étape 2)
---------------------------------

Matériel **BrailleRAP**:

  * 2 barres lisses Ø8mm, longueur : 330mm

Matériel **BrailleRAP XL**:

  * 2 barres lisses Ø8mm, longueur : 470mm

.. NOTE:: Nous n'avons pas représenté la façade pour des raisons de lisibilité.

* Enfiler les barres à mi-course par l’extérieur de la caisse.

.. image :: ./IMG/BrailleRAP-V5.51.1.jpg
       :align: center

* Enfiler le fin de course et son support sur la barre Ø8mm côté face arrière.

.. image :: ./IMG/BrailleRAP-V5.51.2.jpg
       :align: center

.. NOTE:: La vis du support de l'interrupteur sera serrée plus tard lors du réglage.

* Enfiler le chariot bas sur les barres lisses.

.. image :: ./IMG/BrailleRAP-V5.51.3.jpg
       :align: center

|

* Terminer d’enfiler les barres (les barres ne doivent pas dépasser dans le bois de la caisse).
* Serrer les 4 vis des supports d’axes sur la caisse (2 sur le côté gauche et 2 sur le côté droit) et les 4 vis sans tête des supports des axes suffisamment pour que les axes ne coulissent dans leurs logements.

.. image :: ./IMG/BrailleRAP-V5.51.4.jpg
       :align: center

|

Montage de l’axe vertical (étape 1)
------------------------------------

Matériel :

  * **Pièce(s) imprimée(s) en 3D** : 2 X KP08_support
  * 2 KP08
  * 4 vis M5-25
  * 4 rondelles M5
  * 4 écrous M5 NYL

.. NOTE:: Avant de fixer les KP08, s'assurer que les roulements sont bien alignés dans leurs logements. Il se peut qu'ils soient livrés un peu désaxés. Dans ce cas, introduire une barre Ø 8mm et l'actionner manuellement afin de les redresser.

.. image :: ./IMG/BrailleRAP-V5.40.jpg
       :align: center

|

* Visser les KP08_support et les KP08 sur la caisse en laissant un peu de jeu avec les vis M5-25, les rondelles M5 et les écrous M5 NYL.

.. image :: ./IMG/BrailleRAP-V5.34.1.jpg
       :align: center

|

* Respecter la position des bagues de serrage des KP08.

.. image :: ./IMG/BrailleRAP-V5.36.1.jpg
       :align: center

.. image :: ./IMG/BrailleRAP-V5.35.1.jpg
       :align: center

|

Montage de l’axe vertical (étape 3)
------------------------------------

Matériel :

  * 1 barre lisse Ø 8mm, longueur : 100mm
  * 1 Coupleur 5*8mm

* Enfiler le coupleur sur l’arbre du moteur (trou Ø 5mm en bas).

.. image :: ./IMG/BrailleRAP-V5.59.jpg
       :align: center

|

* Enfiler la barre lisse de 100mm depuis le haut à travers les KP08 et dans le coupleur.

.. image :: ./IMG/BrailleRAP-V5.60.1.jpg
       :align: center

|

* Faire tourner l’axe à la main pour s’assurer que tous les éléments sont bien alignés et que l'axe continue à tourner librement.

.. image :: ./IMG/BrailleRAP-V5.60.2.jpg
       :align: center

|

* Les trous du support moteur sont oblongs et permettent d'aligner le moteur avec l'axe vertical dans les 2 dimensions.
* Visser les 2 premières vis du moteur sur son support.

.. image :: ./IMG/BrailleRAP-V5.61.jpg
       :align: center

|

* Visser petit à petit les vis des KP08 en faisant tourner l’axe à la main.
* Visser petit à petit les vis du support moteur sur la caisse en faisant tourner l’axe à la main. **AJOUTER IMAGE**
* Retirer l’axe et terminer de visser les 2 dernières vis du moteur sur son support, puis le support sur la caisse.

Montage de l’axe vertical (étape 4)
------------------------------------

Matériel :

  * 2 poulies GT2 20 dents bore 8mm

* Visser les 2 vis en bas du coupleur sur l’arbre du moteur en s’assurant qu’une des vis est en face du méplat de l’axe du moteur et que le bas du coupleur ne repose pas sur le moteur.

.. image :: ./IMG/BrailleRAP-V5.62.jpg
       :align: center

|

* Enfiler l’axe de 100mm dans les KP08, les poulies (en respectant leurs positions) et le coupleur.

.. image :: ./IMG/BrailleRAP-V5.63.jpg
       :align: center

|

* Visser les 2 vis en haut du coupleur sur l’axe vertical.

.. image :: ./IMG/BrailleRAP-V5.64.jpg
       :align: center

|

* Laisser les poulies libres sans les visser sur l'axe. Elles seront vissées quand la courroie sera en place.
* Visser les vis des bagues de serrage des KP08 (2 vis par bague).

.. image :: ./IMG/BrailleRAP-V5.65.jpg
       :align: center

|

* S’assurer que l’axe tourne aisément et que le moteur n’oscille pas. Le cas échéant, desserrer les vis du moteur et du support sur la caisse pour leur donner du jeu et refaire l’alignement.

Montage de la courroie du chariot bas
--------------------------------------

Matériel **BrailleRAP**:

  * 1 courroie GT2 longueur ± 620mm
  * 2 colliers

Matériel **BrailleRAP XL**:

  * 1 courroie GT2 longueur ± 960mm
  * 2 colliers

* A l’aide d’un collier, attacher la courroie autour de la vis du chariot avec les dents à l’extérieur.

.. image :: ./IMG/BrailleRAP-V6.66.1.jpg
       :align: center

|

* Faire passer la courroie dans la poulie libre puis la poulie de l’axe vertical.

.. image :: ./IMG/BrailleRAP-V6.66.2.jpg
       :align: center

| 

* Tendre la courroie en retenant le chariot et fixer la deuxième extrémité de la courroie sur sa vis avec un collier. 

* Finir de tendre la courroie à l'aide de la vis à l'extérieur de la caisse. 

.. image :: ./IMG/pulley_tensioner_down.jpg
       :align: center

|

.. Note:: Pour l'instant, ne pas serrer les vis de la poulie sur l'axe.

.. image :: ./IMG/BrailleRAP-V5.66.jpg
       :align: center

|
  
Montage de l’axe Y (étape 1)
-----------------------------

Matériel **BrailleRAP**:
  * 2 KFL8
  * 4 vis M5-18
  * 4 écrous M5 NYL
  * 4 rondelles M5
  * 1 poulie GT2 20 dents bore 8mm
  * 1 barre lisse Ø 8mm, longueur : 364mm
  * 1 courroie GT2 fermée 200 mm 

Matériel **BrailleRAP XL**:
  * 2 KFL8
  * 4 vis M5-18
  * 4 écrous M5 NYL
  * 4 rondelles M5
  * 1 poulie GT2 20 dents bore 8mm
  * 1 barre lisse Ø 8mm, longueur : 505mm
  * 1 courroie GT2 fermée 200 mm 
  
* Fixer les KFL8 à gauche sur la caisse avec 2 vis M5-18, 2 rondelles M5 et 2 écrous M5 NYL.

.. image :: ./IMG/BrailleRAP-V5.67.jpg
       :align: center

.. image :: ./IMG/BrailleRAP-V5.68.jpg
       :align: center

|

* Fixer les KFL8 à droite sur la caisse avec les KFL8_support, 2 vis M5-18, 2 rondelles M5 et les 2 écrous M5 NYL.

.. image :: ./IMG/BrailleRAP-V5.69.jpg
       :align: center

.. image :: ./IMG/BrailleRAP-V5.70.jpg
       :align: center

|

* Enfiler la barre lisse à mi course par le côté gauche à travers la caisse et le KFL8.
* Dans l’ordre, enfiler la poulie GT2 20 dents bore 8mm, la courroie fermée et les 3 (A4) ou 4 (XL) ROLL_joint3 (attention à la position du joint torique). Mettre la courroie fermée sur la poulie du moteur Y et sur la poulie de l’axe.

.. image :: ./IMG/BrailleRAP-V5.73.jpg
       :align: center

|

* Enfoncer l’axe dans le KFL8 de droite et le faire traverser pour qu’il dépasse de ±12mm de la caisse.

.. image :: ./IMG/BrailleRAP-V5.74.jpg
       :align: center

|

* Serrer les vis des bagues des KFL8.

.. image :: ./IMG/BrailleRAP-V5.75.jpg
       :align: center

|

Montage de l’axe Y (étape 2)
----------------------------

* Faire tourner à la main la poulie du moteur afin que la poulie de l’axe s’aligne verticalement avec la poulie du moteur.

.. image :: ./IMG/BrailleRAP-V5.76.jpg
       :align: center

.. image :: ./IMG/BrailleRAP-V5.76.1.jpg
       :align: center

|

* Déplacer l’ensemble moteur Y/support le long des trous oblongs sous la caisse afin de tendre la courroie fermée puis serrer les 2 vis.

.. image :: ./IMG/BrailleRAP-V5.77.jpg
       :align: center

|

* Serrer les 2 vis de la poulie de l'axe.

.. image :: ./IMG/BrailleRAP-V5.78.jpg
       :align: center

|

Montage des guide-papiers sur la plaque support
-----------------------------------------------
Matériel :

  * **Pièce(s) imprimée(s) en 3D** : PAPER_GUIDE_left          pour BrailleRAP
  * **Pièce(s) imprimée(s) en 3D** : PAPER_GUIDE_right         pour BrailleRAP
  * **Pièce(s) imprimée(s) en 3D** : paper_guide_left_XL       pour BrailleRAP XL
  * **Pièce(s) imprimée(s) en 3D** : paper_guide_right_XL      pour BrailleRAP XL
  
  * **PAPER_SUPPORT** (contre-plaqué de 5mm découpé au laser)
  * 4 vis M3-16
  * 4 vis M3-14
  * 8 rondelles M3 Larges
  * 8 écrous M3 NYL

.. NOTE:: Les vis M3-16(M3-18 si vous n'avez pas de M3_16) sont utilisées pour les trous ou il y a 2 epaisseurs de bois.

.. NOTE:: C'est à cette étape que ce trouve la principale difference entre une **BrailleRAP** et une **BrailleRAP XL**.

BrailleRAP utilise les pièces PAPER_GUIDE_left et PAPER_GUIDE_right.

.. image :: ./IMG/paper_guide_left.png
       :align: center

.. image :: ./IMG/paper_guide_right.png
       :align: center

|

BrailleRAP XL utilise les pièces paper_guide_left_XL et paper_guide_right_XL.

.. image :: ./IMG/paper_guide_left_A3_v8.png
       :align: center

.. image :: ./IMG/paper_guide_right_A3_v8.png
       :align: center

|

* Partie gauche.

* Assembler les guide-papiers sur la plaque avec les vis M3-16/M3-14, des rondelles M3 Larges et les écrous M3 NYL.

.. image :: ./IMG/paper_support_assembly_screw_v2.png
       :align: center

|

.. image :: ./IMG/paper_support_assembly_v1.png
       :align: center

|

* Répéter l'opération pour la partie droite.

.. image :: ./IMG/paper_support_assembly_right_v1.png
       :align: center

|

* Vérifier que vous pouvez poser une feuille de papier sur le plateau sans que la feuille gondole. Si la feuille gondole, essayez d'écarter les guides papier avant le serrage.

.. image :: ./IMG/paper_support_assembly_papertest_v2.png
       :align: center

|

Collage de la plaque repose papier
-------------------------------------
Matériel :

  * PAPER_support (contre-plaqué de 5mm découpé au laser).
  * 3 Rouleaux papier préparés (avec joint et vis) (4 pour BrailleRAP XL)
  
.. NOTE:: Coller la plaque uniquement si vous êtes sure du montage qui est en dessous. Si vous n'êtes pas sure, vous pouvez vous contenter de positionner la plaque support, vous la collerez à la fin quand l'embosseuse marchera.

* Encoller les encoches qui vont être en contact. Introduire la plaque par l'arrière et la maintenir fermement avec du ruban adhésif pendant le temps de séchage.

.. image :: ./IMG/BrailleRAP-V6.96.jpg
       :align: center

.. image :: ./IMG/BrailleRAP-V5.97.jpg
       :align: center

.. image :: ./IMG/BrailleRAP-V5.98.jpg
       :align: center

|

Montage du chariot haut (étape 2)
---------------------------------
Matériel **BrailleRAP**:

  * 2 barres lisses Ø 8mm, longueur : 330mm

Matériel **BrailleRAP XL**:

  * 2 barres lisses Ø 8mm, longueur : 470mm

* Enfiler les barres à mi-course par l’extérieur de la caisse.

.. image :: ./IMG/BrailleRAP-V5.89.jpg
       :align: center

|

* Enfiler le chariot haut sur les barres lisses.

.. image :: ./IMG/BrailleRAP-V5.90.jpg
       :align: center

|

* Terminer d’enfiler les barres.

.. Note:: La tranche du bois doit rester apparente.

.. image :: ./IMG/BrailleRAP-V5.91.jpg
       :align: center

|

* Serrer les vis des supports d’axes sur la caisse à gauche et à droite.

.. image :: ./IMG/BrailleRAP-V5.92.jpg
       :align: center

|

* Visser les vis sans tête des supports des axes à gauche et à droite.

.. image :: ./IMG/BrailleRAP-V5.93.jpg
       :align: center

|

Pose de la courroie du chariot haut
--------------------------------------

Matériel **BrailleRAP**:

  * 1 courroie GT2 longueur ± 620mm
  * 2 colliers

Matériel **BrailleRAP XL**:

  * 1 courroie GT2 longueur ± 620mm
  * 2 colliers

* A l’aide d’un collier, attacher la courroie autour de la vis du chariot avec les dents à l’extérieur.

.. image :: ./IMG/BrailleRAP-V6.66.1.jpg
       :align: center

|

* Faire passer la courroie dans la poulie libre puis la poulie de l’axe vertical.

.. image :: ./IMG/BrailleRAP-V6.66.2.jpg
       :align: center

|

* Tendre la courroie en retenant le chariot et fixer la deuxième extrémité de la courroie sur sa vis avec un collier. 

* Finir de tendre la courroie à l'aide de la vis à l'extérieur de la caisse. 

.. image :: ./IMG/pulley_tensioner_up.jpg
       :align: center

|

Montage des presse-papiers (étape 2) :
----------------------------------------
Matériel **BrailleRAP**:

  * 3 CLIPBOARD montés à l'étape 1
  * 6 vis M3-14
  * 6 rondelles M3 Larges
  * 6 écrous M3 NYL

Matériel **BrailleRAP XL**:
  
  * 4 CLIPBOARD montés à l'étape 1
  * 8 vis M3-14
  * 8 rondelles M3 Larges
  * 8 écrous M3 NYL

.. NOTE:: Les trous oblongs dans les pièces imprimées permettent de régler la pression des CLIPBOARD sur le papier.

.. image :: ./IMG/BrailleRAP-V6.104.jpg
       :align: center

.. image :: ./IMG/BrailleRAP-V6.105.jpg
       :align: center

|

Montage du fin de course Y 
------------------------------

Matériel :

  * **Pièce(s) imprimée(s) en 3D** : ENDSTOP_Y_support, ENDSTOP_Y_lever_weight
  * 2 vis M3-14
  * 2 vis M3-12
  * 1 vis M3-20
  * 2 rondelles M3 Larges
  * 3 écrous M3 NYL
  * 2 écrous M3 
  * 1 interrupteur fin de course à lamelle
  * 2 vis M2.5-14
  * 2 écrous M2.5 NYL

.. NOTE:: On utilisera de preference un endstop avec le cable coudé.

.. image :: ./IMG/endstop_coude.jpg
       :align: center

* Tarauder le support de la vis de reglage avec un taraud M3

.. image :: ./IMG/BrailleRAP-V6.106.png
       :align: center

|

* Positionner le levier **ENDSTOP_Y_LEVER** dans le support **ENDSTOP_Y_support**.

.. image :: ./IMG/BrailleRAP-V6.106.1.png
       :align: center

|

* Fixer le levier **ENDSTOP_Y_LEVER** au support **ENDSTOP_Y_support** avec une vis M3-20 et un écrou M3-NYL

.. NOTE:: Ne pas serrer l'ecrou M3, le levier doit pouvoir tourner librement dans son support.

.. image :: ./IMG/BrailleRAP-V6.106.2.png
       :align: center
.. image :: ./IMG/BrailleRAP-V6.106.3.png
       :align: center

|

* Assembler l'interrupteur fin de course et le **ENDSTOP_Y_support** à l'aide des vis M2.5-14 et des écrous M2.5 NYL.

.. image :: ./IMG/BrailleRAP-V6.106.4.png
       :align: center
.. image :: ./IMG/BrailleRAP-V6.106.5.png
       :align: center

|

* Positionner la vis de reglage M3-12 sur le levier **ENDSTOP_Y_LEVER_weight**

.. image :: ./IMG/BrailleRAP-V6.106.6.png
       :align: center

|

* Ajouter un écrou M3-NYL, 2 écrou m3 et une vis M3-12 sur le levier **ENDSTOP_Y_LEVER_weight**

.. image :: ./IMG/BrailleRAP-V6.106.7.png
       :align: center

|

* Assembler l'ensemble interrupteur fin de course et le **ENDSTOP_Y_support** sur la caisse à l'aide des vis M3-14, des rondelles M3 et des écrous M3 NYL.

.. image :: ./IMG/BrailleRAP-V6.107.jpg
       :align: center

.. image :: ./IMG/BrailleRAP-V6.108.jpg
       :align: center

|

Fixation des clips sur le couvercle
-----------------------------------
Matériel :

  * **Pièce(s) imprimée(s) en 3D** : 2 LID_LOCK
  * 4 vis M3-14
  * 4 écrous M3 NYL

* Assembler les 2 LID_LOCK sur le couvercle à l'aide des vis M3-14, des rondelles M3 et des écrous M3 NYL.

.. image :: ./IMG/BrailleRAP-V5.110.jpg
       :align: center

.. image :: ./IMG/BrailleRAP-V5.111.jpg
       :align: center

|

Fixation de la plaque pour l'embase de l'alimentation
-----------------------------------------------------
Matériel :

  * **Pièce(s) imprimée(s) en 3D** : POWER_plate
  * 2 vis M3-14
  * 2 écrous M3 NYL

.. image :: ./IMG/alim.jpg
       :align: center

|

Preparation des cables moteurs
------------------------------

* 2 cables moteurs XH 2.54 4 pins => 6 pins

Vérifier le schéma de cablage des cables. le cablage est le suivant

========== ===========
coté carte coté moteur
========== ===========       
1          1
2	    4
3	    6
4	    3
========== ===========

.. image :: ./IMG/cablagemoteur.jpg
       :align: center

|

Montage de la carte électronique MKS 1.4
----------------------------------------
Matériel :

  * Carte MKS GEN 1.4
  * 4 entretoises M3-12
  * 4 rondelles M3 Larges
  * 8 vis M3-8

* Assembler les 4 entretoises sur la carte. 

.. NOTE:: Pour pouvoir réaliser les derniers réglages facilement, nous vous conseillons de cabler la carte en dehors du chassis. Une fois l'embosseuse fonctionelle, vous pourrez fixer la carte dans le chassis.

|

Cablage de la carte électronique MKS 1.4
----------------------------------------
Schéma général :

.. image :: ./IMG/braillerap_cablage.png
       :align: center

|

Photo de la carte assemblée

.. image :: ./IMG/braillerap_carte.jpg
       :align: center

|

Pose des drivers sur la carte électronique
------------------------------------------
Matériel :

  * Carte MKS GEN 1.4
  * 2 Drivers DRV8825
  * 6 cavaliers

* Si la carte ne vous est pas fournie déjà équipée de cavaliers, en mettre aux emplacements des drivers des moteurs X et Y.

.. image :: ./IMG/brap_cavalier.png
       :align: center

|

* Enfoncer les drivers dans les emplacements X et Y.

.. image :: ./IMG/brap_drivers.png
              :align: center

|

Câblage de l'alimentation 12V
-----------------------------
* placer les 2 fils de provenant de la prise **POWER_plate** dans le bornier de la carte MKS

.. image :: ./IMG/board_12v.jpg
              :align: center

|

Réglage des drivers moteur
--------------------------
.. NOTE:: Cette étape doit **IMPERATIVEMENT** être réaliser **avant** le cablage des moteurs.

* Controler que vous pouvez brancher l'alimentation 12V sur la carte (un dernier controle pour eviter des etincelles c'est mieux :-) )
* Brancher l'alimentation 12 V sur la carte.
* pour chaque driver, mesurer, avec un multimètre, la tension entre le potentiomètre de réglage et la masse de la connexion USB.

.. image :: ./IMG/mks_driver_voltage.jpg
              :align: center
.. image :: ./IMG/mks_driver_voltage1.jpg
              :align: center
.. image :: ./IMG/mks_driver_voltage2.jpg
              :align: center
.. image :: ./IMG/mks_driver_voltage3.jpg
              :align: center

|

* La tension mesurée doit être proche de 0,6 V pour des drivers DRV8825, si ce n'est pas le cas, utiliser un tournevis pour tourner le potentiomêtre de réglage et refaite la mesure.
* Une fois que la tension mesurée sur chaque driver est correcte, vous pouvez passer à la suite

Câblage des interrupteurs fin de course
---------------------------------------
* Cabler les fins de courses sur la carte.
* Le fin de course X (chariot) doit être branché sur le connecteur de gauche (rouge)
* Le fin de course Y (détection papier) doit être branché sur le connecteur de gauche (bleu)

.. image :: ./IMG/board_endstop.jpg
              :align: center

|

Raccordement des moteurs à la carte
------------------------------------
* Relier les moteurs à la carte de contrôle avec les cables.
* Le moteur X (chariot) doit être branché dans le connecteur de gauche (rouge)

.. image :: ./IMG/brap_motorx.jpg
              :align: center

|

* Le moteur Y (papier) doit être branché dans le connecteur de droite (bleu)

.. image :: ./IMG/brap_motory.jpg
              :align: center

|

Câblage de l’électro-aimant
---------------------------
* placer les 2 fils de l'electroaimant et la diode de roue libre. Attention au sens de la diode (trait blanc).

.. image :: ./IMG/board_magnet.jpg
       :align: center

|

Montage de la carte électronique MKS GEN-L V2.1
-----------------------------------------------
Matériel :

  * Carte MKS GEN L V2.1
  * 4 entretoises M3-12
  * 4 rondelles M3 Larges
  * 8 vis M3-8

* Assembler les 4 entretoises sur la carte. 

.. NOTE:: Pour pouvoir réaliser les derniers réglages facilement, nous vous conseillons de cabler la carte en dehors du chassis. Une fois l'embosseuse fonctionelle, vous pourrez fixer la carte dans le chassis.

|

Cablage de la carte électronique MKS GEN-L V2.1
-----------------------------------------------
Schéma général :

.. image :: ./IMG/mksgenl_schema.png
       :align: center

|

Photo de la carte assemblée

.. image :: ./IMG/mksgenl.jpg
       :align: center

|

Pose des drivers sur la carte électronique MKS GEN-L V2.1
---------------------------------------------------------
Matériel :

  * Carte MKS GEN-L V2.1
  * 2 Drivers DRV8825
  * 6 cavaliers

* Si la carte ne vous est pas fournie déjà équipée de cavaliers, en mettre aux emplacements des drivers des moteurs X et Y.

.. image :: ./IMG/mksgenl_jumper.jpg
       :align: center

|

* Enfoncer les drivers dans les emplacements X et Y.

.. image :: ./IMG/mksgenl_drivers.jpg
              :align: center

|

Câblage de l'alimentation 12V
-----------------------------
* placer les 2 fils de provenant de la prise **POWER_plate** dans le bornier de la carte MKS GEN-L

.. image :: ./IMG/mksgenl_12V.jpg
              :align: center

|

Réglage des drivers moteur
--------------------------
.. NOTE:: Cette étape doit **IMPERATIVEMENT** être réaliser **avant** le cablage des moteurs.

* Controler que vous pouvez brancher l'alimentation 12V sur la carte (un dernier controle pour eviter des etincelles c'est mieux :-) )
* Brancher l'alimentation 12 V sur la carte.
* pour chaque driver, mesurer, avec un multimètre, la tension entre le potentiomètre de réglage et la masse de la connexion USB.

.. image :: ./IMG/mks_driver_voltage.jpg
              :align: center
.. image :: ./IMG/mks_driver_voltage1.jpg
              :align: center
.. image :: ./IMG/mks_driver_voltage2.jpg
              :align: center
.. image :: ./IMG/mks_driver_voltage3.jpg
              :align: center

|

* La tension mesurée doit être proche de 0,6 ~ 0,7 V pour des drivers DRV8825, si ce n'est pas le cas, utiliser un tournevis pour tourner le potentiomêtre de réglage et refaite la mesure.
* Une fois que la tension mesurée sur chaque driver est correcte, vous pouvez passer à la suite

Câblage des interrupteurs fin de course
---------------------------------------
* Cabler les fins de courses sur la carte MKS GEN-L.
* Le fin de course X (chariot) doit être branché sur le connecteur de gauche en haut (rouge)
* Le fin de course Y (détection papier) doit être branché sur le connecteur de gauche en bas (bleu)

.. image :: ./IMG/mksgenl_endstops.jpg
              :align: center

|

Raccordement des moteurs à la carte MKS GEN-L
---------------------------------------------
* Relier les moteurs à la carte de contrôle avec les cables.
* Le moteur X (chariot) doit être branché dans le connecteur de gauche (rouge)

.. image :: ./IMG/mksgenl_motorx.jpg
              :align: center

|

* Le moteur Y (papier) doit être branché dans le connecteur de droite (bleu)

.. image :: ./IMG/mksgenl_motory.jpg
              :align: center

|

Câblage de l’électro-aimant MKS GEN-L 2.1
-----------------------------------------
* placer les 2 fils de l'electroaimant sur le connecteur HBED de la carte MKS GEN-L 2.1.

.. image :: ./IMG/mksgenl_solenoid.jpg
       :align: center

|

Alignement horizontal de l'empreinte du chariot haut
----------------------------------------------------
* Dé serrer la poulie sur l’axe vertical pour libérer le chariot supérieur.

.. image :: ./IMG/toppulley_fix.jpg
       :align: center

|

* Aligner les 2 chariots
* Déplacer le chariot supérieur pour aligner l'empreinte (**FEMALE_shape**) avec le sommet du pointeau.
* Utiliser les vis de fixation de la **FEMALE_shape** pour aligner l'empreinte avec le sommet du pointeau.
* Quand l'alignement est satisfaisant, serrer les vis de fixations de la **FEMALE_shape**.

.. image :: ./IMG/female_fix1.jpg
       :align: center
.. image :: ./IMG/female_fix2.jpg
       :align: center

|

Alignement vertical des deux chariots
--------------------------------------

* Dé serrer la poulie du chariot supérieur sur l’axe vertical pour libérer le chariot supérieur.

.. image :: ./IMG/toppulley_fix.jpg
       :align: center

|

* En observant par l'arriere de la machine, monter le pointeau en appuyant avec le doigt sous l'electro-aimant.
* Déplacer le chariot supérieur pour aligner l'empreinte (**FEMALE_shape**) avec le sommet du pointeau.
* Logiquement le pointeau doit entrer légérement dans la vis sans tête de la **FEMALE_shape**.

.. image :: ./IMG/magnet_align.jpg
       :align: center

|

* Quand l'alignement est satifaisant, verouiller la poulie supérieure sur l'axe vertical.

.. image :: ./IMG/toppulley_fix.jpg
       :align: center

|

Ajustement des capteurs de fin de course chariot et papier (X et Y)
-------------------------------------------------------------------

* Ajuster la position du capteur fin de course X. Le capteur doit s'activer avant que la fixation de la courroie du chariot bas rencontre la poulie inférieure de l'axe verticale.

* Avec une feuille de papier, ajuster le fin de course Y pour que le capteur s'active quand une feuille est présente sous le levier du capteur. Et se désactive si la feuille de papier n'a pas encore déplacée le levier.

.. image :: ./IMG/endstopy_adjust.jpg
       :align: center

|

Réglage de la profondeur du point
---------------------------------

* Selon le matériau que vous utiliserez (papier, plastique, aluminium de canette), vous devrez régler la hauteur de l'empreinte du chariot haut à l'aide de l'écrou borgne. *

.. image :: ./IMG/BrailleRAP-V5.112.jpg
       :align: center

|

Fermeture de la porte arriere
-----------------------------
Matériel :

  * **Pièce(s) imprimée(s) en 3D** : 2 DOORLOCKER.stl
  * 4 vis M3-16

  * Tarauder les trous de fixation des pieces **DOORLOCKER**

  .. image :: ./IMG/DOORLOCK_tap.png
       :align: center

  * Attacher les **DOORLOCKER** sur la porte arriere. Laisser du jeu pour que les pieces **DOORLOCKER** puissent coulisser.

  .. image :: ./IMG/door_locker.png
       :align: center

  * Positionner la porte assemblée sur BrailleRAP. 
  * Faire glisser les pieces **DOORLOCKER** sur les trous de fixation pour que la porte soit bloquée.
  * Serrer (doucement) les vis de fixation.

|

Réglage fin des marges X et Y
-----------------------------

En utilisant un logiciel comme pronterface, vous pouvez ajuster la distance entre les fins de courses et la position 0 sur le papier. C'est particulièrement utile pour BrailleRAP XL.
Les fins de courses sont en dehors du papier, par consequent l'offset doit toujours être négatif.

la reference de la commande est disponible ici : '<https://marlinfw.org/docs/gcode/M206.html>'_

pour connaitre les valeurs des offsets:

M206

pour régler l'offset X :

M206 X-xx.xx

pour régler l'offset Y :

M206 Y-xx.xx

Pour sauvegarder ces valeurs en EEPROM utiliser la commande :
M500

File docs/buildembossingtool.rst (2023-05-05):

Building the embossing tool
===========================

Material
--------

The embossing tool is made of an M3 screw, machined with a dremel like tool.

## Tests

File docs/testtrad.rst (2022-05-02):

Test de traduction avec outils sphinx
=====================================

est ce que 'RTFD'genere correctement les fichiers .po ?

est que la modif des po suffit ?

for test only in the original .po

blob
----

ksldjl klsjdlqsk jlkq jdlqsjd qlljsdljqs ljdqlsjdqsldjql

essai
-----
qdqdlqjl jlkqdjqljdqs  slj qlsjqsl  slqdj dqlsjd  qs jqljdqsl   qsqjqljqjdqls

.

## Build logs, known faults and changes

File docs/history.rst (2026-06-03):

Historique du projet
====================

Le commencement
---------------

En 2016 l'association **MyHumanKit** organise en collaboration avec **Airbus Industries** un hackaton appelé Fabrikarium. 

Pendant le Fabrikarium plusieurs travaux ont été réalisés pour modifier des imprimantes 3D afin d'embosser du **Braille** sur du papier 160g, 

Le projet s'appelait `BrailleRap <https://github.com/arthursw/BrailleRap/blob/master/Documentation/documentation-en.md>`_.

Dans l'equipe BrailleRAP-SP nous pensions que ces travaux êtaient une démonstration de faisabilité, 
mais qu'il fallait mettre au point une machine spécialisée facile à reproduire.

OpenBraille
-----------
En 2017 Carlos Campos démarre le projet OpenBraille et construit une embosseuse braille à partir de pièces d'imprimante recyclées. 

Le projet démontre qu'il est possible de déplacer une feuille de papier avec suffisamment de précision dans une embosseuse braille. 

BrailleRap-SP
-------------
En Janvier 2018, nous avons commencé avec quelques rails linéaires, des moteurs Nema et des pièces imprimées pour essayer de réaliser une embosseuse Braille. Quelques essais plus tard, nous avons commencé à montrer des exemples de textes embossés en Braille, et tout le monde était très enthousiastes. Le projet BrailleRAP-SP était né.  

BrailleRap
----------
En 2022, pour pouvoir continuer le projet avec quelques enthousiastes, nous reprenons le projet pour proposer des améliorations.

BrailleRap Cameroun
-------------------
Toujours en 2022, le CCLab nous confie la préparation et la réalisation de 4 ateliers grand public au Cameroun. C'est l'opération BrailleRAP Cameroun. 

2 ateliers grand public, 2 master class dans 4 villes du Cameroun en collaboration avec l'ANIAAC, l'Association National pour l'Intégration et l'Accomodation des Aveugles du Cameroun.
C'est l'occasion pendant 3 semaines, de confronter une nouvelle fois le projet au grand public: non voyants, makers, associations, établissements d'enseignements. Tout cela dans un contexte international très différent de nos activités habituelles.

Une experience riche en rencontres exceptionelles, en anecdotes, en expérimentations et en nouvelles idées d'évolutions et d'améliorations.

Hackaday Prize
--------------
Riche de l'experience du Cameroun, des améliorations sont apportées :

* Création du logiciel `AccessBrailleRAP <https://github.com/braillerap/AccessBrailleRAP>`_ en utilisant la bibliotheque open source `liblouis <https://liblouis.io/>`_ ce qui améliore considérablement la transcription Braille et ouvre la possibilité d'avoir un logiciel utilisable avec un lecteur d'écran.
* Renforcement des supports moteurs pour faciliter le transport.
* Déplacement du fin de course de détection du papier pour faciliter le réglage.
* Ajout d'un rouleau d'entrainement du papier supplémentaire pour permettre l'utilisation de différent format de support.

Courant 2023, le projet est présenté au concours international `HackadayPrize <https://hackaday.com/2023/11/07/hackaday-prize-2023-ending-10-years-on-a-high-note/#more-639760>`_ et remporte le 5° prix à Pasadena le 7/11/2023. L'intégralité du prix associé est consacré au développement d'un prototype d'utilisation de la BrailleRAP à partir d'un téléphone portable. 

.. raw:: html

    <div style="position: relative; padding-bottom: 5%; overflow: hidden; max-width: 100%; height: auto;">
	    <iframe width="560" height="315" src="https://www.youtube.com/embed/afmmY3M2pTo?si=0mn0qBLbHShMuEfu&amp;controls=0" title="YouTube video player" frameborder="0" allow="accelerometer; autoplay; clipboard-write; encrypted-media; gyroscope; picture-in-picture; web-share" referrerpolicy="strict-origin-when-cross-origin" allowfullscreen></iframe>
    </div>

Ateliers intensifs et financement
---------------------------------
Le prix international renforce la notoriété du projet, c'est l'occasion de préparer une dizaine d'ateliers et masterclass à travers la France mais aussi en Belgique et en République Démocratique du Congo.

* Des ateliers "grand public" pour sensibiliser à l'utilisation des techniques de Fablab et equiper une famille (coucou Sophie et Noé), des institutions (une fédération d'office de tourisme, un musée, une médiathèque et une mairie).
* Des master class pour demystifier la complexité du montage de la machine et former les fabmanagers a l'assemblage et à la maintenance, avec l'objectif de leur faciliter l'animation d'atelier.

Autant d'expériences qui font évoluer à la fois les scénari de conduite d'ateliers. Mais également le modèle et améliore la facilité de montage en atelier, la maintenance, la vitesse d'embossage et les réglages. C'est egalement la naissance du premier modèle A3, la BrailleRAP XL.

En paralelle nous déposons un dossier de financement auprès de la fondation `NlNet <https://nlnet.nl/project/BrailleRAP/>`_. Financement que la fondation nous a accordé. C'est le premier financement suivi dans le temps, il nous permet de développer les premières versions de `DesktopBrailleRAP <https://github.com/braillerap/DesktopBrailleRAP>`_ et `OpenStreetTouch <https://github.com/braillerap/OpenStreetTouch>`_ . L'occasion également de poursuivre des `expérimentations <https://github.com/braillerap/DesktopBrailleRAP/wiki/Pattern-filling-test-%E2%80%90-the-method>`_ avec des publics non ou mal voyant mais aussi des associations.

Certification open hardware
---------------------------

Après une année chargée, notamment avec les ateliers au Congo et en Belgique, la création du modèle XL et de nombreuses heures consacrées au développement de DesktopBrailleRAP et OpenStreetTouch, et des discussions autours du modèle de licence open source. A l'été 2025, durant la conférence `Dinacon <https://2025.dinacon.org/>`_ nous déposons un dossier de certification auprès de l' `OSHWA <https://oshwa.org/>`_. Le 17 Juillet 2025 le dossier est accepté, et BrailleRAP est désormais certifié Open Source Hardware.

.. image :: ./IMG/BrailleRAP-cert-oshwa.png
  :width: 400px
  :align: center

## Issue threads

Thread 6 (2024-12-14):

Merge readthedocs French and English sites

DeflateAwning, 2024-12-14:
I'm having trouble figuring out how to contribute to the English BrailleRAP readthedocs. They seem to be stored somewhat as a translation, but are hosted on their own sites (i.e., at `https://braillerap-en.readthedocs.io/` instead of `https://braillerap.readthedocs.io/en`.

Would appreciate more info about these, and think that maybe the two sites should be merged.

crocsg, 2024-12-15:
There is a little bit of history in that. When we started the documentation on readthedoc there was no very clear way to make multilingual documentation project. Since readthedoc use python Sphynx, we translated the french documentation with Sphynx and build a separate project for the english version. Beside the 2 url i have many concern about this process.
- The documentation structure is defined in French. For years it was not a problem as most of BrailleRAP builder where French locutor. Things have changed in the past few month.
- To get effective translation in a language, you need to build a Sphynx pipeline somewhere. This is not a problem for Python user, but it is obviously a bottleneck in new translation contribution.
- As the project evolve, it's becoming more and more difficult to well document some of the device options. I made something with BrailleRAP and BrailleRAP XL, but i have some experiment working with different kind of controller board and would like to publish it without disturbing new BrailleRAP builders. There is also some experiment around the worlds (indonesian guys build some with a complete redesign of the left and right frame just printed on bambulab 3d printer, the guys are not very aware of git and i'm still working to have all that experiment published and "linked" to the BrailleRAP project.
- The actual documentation structure as been refined in public workshop to build the device. It's quite nice for workshop animation, but maybe not the best one for a new BrailleRAP enthusiast.

So i agree, we need to change the documentation, something more modular, more user friendly and make it easier to have new languages. I had a great experiment with weblate on codeberg and BrailleRAP softwares. It's a little different to translate full text than software label, but i'm curious to give it a try. It seem that there is some work to do, maybe not as much as i think, but at this time i'm focused on BrailleRAP softwares (and there will be a software documentation subject at the corner). Maybe it would be a good idea to start a new documentation project, starting with resources from the actual one, and change the background process.  As soon as we are ok with the new process, it's easy to make it the "official" documentation of the project

And just for technical precision, the documentation in french is located in .rst at ./doc the en translation is located at ./doc/locale/en/LC_MESSAGES the .pot needed for gettext are at ./doc/_build/gettext

DeflateAwning, 2024-12-16:
It seems like the `_build/` folder should be in the gitignore. It's not really standard to version control build products.

I'd recommend picking a documentation system that's a bit simpler. Maybe just having the documentation is Markdown files, so they can be viewed directly with git? And then the translations are just completely rewriting each file in a given locale?

crocsg, 2024-12-16:
It seem a bunch of file in git repo will not serve the purpose. Has i've already said, 80% of the BrailleRAP community just don't know what git is

crocsg, 2024-12-16:
Close this until some time and resources to find a better alternative than readthedoc

DeflateAwning, 2024-12-17:
Where's this community you speak of? You didn't even have Issues turned on, and there's no other communication channel on any resources.

No one know how git/github work when they're born. Using them is the way you learn. I'm not sure why you're so afraid of people seeing git being used well, and then learning how to use it themselves. Strange.

I was suggesting that you _store_ the docs in Git and serve them on a website, if you're trying to avoid git.

I suggest reopening the issue as a place to centralize discussion about this; alternatively, you can make a new Issue and move the discussion there.

GitHub Pages is probably your best bet, if you want to move off of readthedocs. GitHub Pages serves the documentation like a regular website, and is built from CI actions in GitHub (which I'd be happy to help setup, if you'd like). Or did you have other ideas?

crocsg, 2024-12-19:
Maybe some life exists outside of github, who knows ?

> I suggest reopening the issue as a place to centralize discussion about this; alternatively, you can make a new Issue and move the discussion there.

Good idea, i've just one old brain, and feel uncomfortable to handle the same discussion over three different channels.

What i suggest is to discuss about the goals a little before jumping on the first pretty technology. Has everybody, i guess you are not happy to work on something, and put it in the bin because you miss the goal.

 If you try to get some information about this projects, you will find that
- Some of our great contributors are unsighted, github is not truly accessible, and you can't really use it only with the command line. But they can do something that i guess you can't, read Braille with their fingers, have some valuable opinion about the quality of documents produced by the device. That's one of the paradox of BrailleRAP, we are designing devices for unsighted peoples, and we just absolutely need them to qualify the device.
- Some of our contributors are far away from IT techs, because they are teachers, sociologists or NGO volunteers. they don't give a shit about git or github, just because they fight everyday to get unsighted children at school learning some Braille. Can you answer the following questions ? Is a BrailleRAP suitable for  usage in school ? and in a Museum ? How is it difficult to build one in Europe or India ? and in the middle of Africa , in Brasil or in Philipina ? Where i can find the 3d model to repair a BrailleRAP built 2 years ago ?
- Some of them "just" contribute with translations via weblate. You can write in english, what about Italian, Helenic, Arabic or Chinese ? Is there some interests to have a building manual in Nepalese or Romanian ? in pdf ? on a mobile ?

In conclusion, take a rest, take some time to think about all that. Any technical contribution would be helpful, but only if they are serving the right goals. And if this project is not fancy enough to put all the tech you are dreaming to use, this is not a problem, this is just the life.  Github is full of projects who need great expertise you can contribute on.

Closed 2024-12-26.

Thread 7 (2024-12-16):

Discussion: How are you making git commits to the main branch? You're creating duplicate commits each time

DeflateAwning, 2024-12-16:
How are you making git commits to the main branch? You're creating duplicate commits (same commit message, but twice) each time. You might have an easier time with git if you refine that process, and it'll make the change history in this repository cleaner too.

Happy to help advise!

crocsg, 2024-12-16:
May i suggest you to analyze the complete commit log  and make some proposal.

DeflateAwning, 2024-12-17:
Well, these are the two ways you're supposed to use git:

### Option 1: GitHub Desktop

1. Download github desktop
2. Clone the repository
3. Pull the latest version of the master branch, if you intend to commit directly to the master branch
4. Make some changes to the cloned files
5. Commit to the master branch
6. Push

### Option 2: Git CLI (Command Line Interface)

1. Clone the repo: `git clone <link to repo>`
2. Pull the latest version of the master branch: `git pull`
3. Make some changes to the files
4. Stage all changed files: `git add .`
5. Commit: `git commit -m "Description of changes goes here"`
6. Push: `git push`

Doing either of those options will avoid the very strange commit patterns you have going on currently

Closed 2024-12-26.

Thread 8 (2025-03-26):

carte MKS tinyBEE non compatible

Cdriko, 2025-03-26:
Bonjour
J'ai essayé d'installer le firmware marlin/braillerap LA CARTE MAKERBASE TINYBEE v1
sans succès : ce firmware ne connais pas la tinybee.
Pourtant la doc annonce cette carte comme compatible :  "Une carte MKS TinyBee (ESP32) et 2 drivers TMC2209 https://github.com/makerbase-mks" [est écrit ici](Une carte MKS TinyBee (ESP32) et 2 drivers TMC2209 https://github.com/makerbase-mks)

J'ai essayé de modifier le Marlin officiel de mks pour le rendre compatible avec le logiciel d'embossage sans succès. il n'a pas l'air de vouloir de la vitesse de connexion à 250000. De plus la configuration des Gcodes M3 M4 eest compliquée par la nouvelle architechture.

quuelqu'un at-il un code qui fonctionne sur cette plateforme ?

merci

crocsg, 2025-03-26:
Bonjour,
pour la MKS TinyBee il faut prendre le firmware marlin2 [https://github.com/braillerap/MarlinBraille2](https://github.com/braillerap/MarlinBraille2), la configuration pour la tinybee est ici [https://github.com/braillerap/MarlinBraille2Configuration](https://github.com/braillerap/MarlinBraille2Configuration)
Ce n'est pas le firmware le plus facile a installer, c'est pour ca que la doc n'est pas au top

Cdriko, 2025-03-26:
Merci de ton aide. J'ai récupéré Marlin 2 et copié les fichiers de configs pour la tinybee mais la compilation plante  :
``` platformio run --silent -e mks_tinybee ; echo "done" >|"/tmp/ipc"
Marlin/src/inc/Warnings.cpp:59:4: warning: #warning "Warning! Don't use dummy thermistors (998/999) for final build!" [-Wcpp]
   #warning "Warning! Don't use dummy thermistors (998/999) for final build!"
    ^
Marlin/src/inc/Warnings.cpp:63:4: warning: #warning "Your Configuration provides no method to acquire user feedback!" [-Wcpp]
   #warning "Your Configuration provides no method to acquire user feedback!"
    ^
cc1plus: warning: unrecognized command line option '-Wno-register'
Marlin/src/module/motion.cpp: In function 'void homeaxis_paperload(AxisEnum)':
Marlin/src/module/motion.cpp:2298:7: warning: variable 'ends' set but not used [-Wunused-but-set-variable]
   int ends = Endstops::Endstops::state();
       ^
Marlin/src/module/motion.cpp:2318:13: warning: unused variable 'axis_home_dir' [-Wunused-variable]
   const int axis_home_dir =  home_dir(axis);
             ^
At global scope:
cc1plus: warning: unrecognized command line option '-Wno-register'
Marlin/src/module/temperature.cpp:2741:34: warning: unknown option after '#pragma GCC diagnostic' kind [-Wpragmas]
   #pragma GCC diagnostic ignored "-Wimplicit-fallthrough"
                                  ^
Marlin/src/module/temperature.cpp: In static member function 'static void Temperature::isr()':
Marlin/src/module/temperature.cpp:3600:36: warning: unknown option after '#pragma GCC diagnostic' kind [-Wpragmas]
     #pragma GCC diagnostic ignored "-Wimplicit-fallthrough"
                                    ^
At global scope:
cc1plus: warning: unrecognized command line option '-Wno-register'
In file included from .pio/libdeps/mks_tinybee/AsyncTCP_RP2040W/src/AsyncPrinter.h:51:0,
                 from .pio/libdeps/mks_tinybee/AsyncTCP_RP2040W/src/AsyncPrinter.cpp:51:
.pio/libdeps/mks_tinybee/AsyncTCP_RP2040W/src/AsyncTCP_RP2040W.h:73:4: error: #error For RASPBERRY_PI_PICO_W board using CYW43439 WiFi only
   #error For RASPBERRY_PI_PICO_W board using CYW43439 WiFi only
    ^
In file included from .pio/libdeps/mks_tinybee/AsyncTCP_RP2040W/src/AsyncTCP_RP2040W.cpp:104:0:
.pio/libdeps/mks_tinybee/AsyncTCP_RP2040W/src/AsyncTCP_RP2040W.h:73:4: error: #error For RASPBERRY_PI_PICO_W board using CYW43439 WiFi only
   #error For RASPBERRY_PI_PICO_W board using CYW43439 WiFi only
    ^
In file included from .pio/libdeps/mks_tinybee/AsyncTCP_RP2040W/src/AsyncTCP_RP2040W_buffer.h:60:0,
                 from .pio/libdeps/mks_tinybee/AsyncTCP_RP2040W/src/AsyncTCP_RP2040W_buffer.cpp:58:
.pio/libdeps/mks_tinybee/AsyncTCP_RP2040W/src/AsyncTCP_RP2040W.h:73:4: error: #error For RASPBERRY_PI_PICO_W board using CYW43439 WiFi only
   #error For RASPBERRY_PI_PICO_W board using CYW43439 WiFi only
    ^
In file included from .pio/libdeps/mks_tinybee/AsyncTCP_RP2040W/src/SyncClient.cpp:53:0:
.pio/libdeps/mks_tinybee/AsyncTCP_RP2040W/src/AsyncTCP_RP2040W.h:73:4: error: #error For RASPBERRY_PI_PICO_W board using CYW43439 WiFi only
   #error For RASPBERRY_PI_PICO_W board using CYW43439 WiFi only
    ^
In file included from /home/cedric/.platformio/packages/framework-arduinoespressif32/tools/sdk/include/lwip/lwip/opt.h:51:0,
                 from /home/cedric/.platformio/packages/framework-arduinoespressif32/tools/sdk/include/lwip/lwip/ip_addr.h:40,
                 from /home/cedric/.platformio/packages/framework-arduinoespressif32/tools/sdk/include/tcpip_adapter/tcpip_adapter.h:45,
                 from /home/cedric/.platformio/packages/framework-arduinoespressif32/tools/sdk/include/esp32/esp_event_legacy.h:23,
                 from /home/cedric/.platformio/packages/framework-arduinoespressif32/tools/sdk/include/esp_event/esp_event.h:26,
                 from /home/cedric/.platformio/packages/framework-arduinoespressif32/tools/sdk/include/esp32/esp_event_loop.h:22,
                 from /home/cedric/.platformio/packages/framework-arduinoespressif32/libraries/WiFi/src/WiFiGeneric.h:27,
                 from /home/cedric/.platformio/packages/framework-arduinoespressif32/libraries/WiFi/src/WiFiSTA.h:28,
                 from /home/cedric/.platformio/packages/framework-arduinoespressif32/libraries/WiFi/src/WiFi.h:32,
                 from .pio/libdeps/mks_tinybee/AsyncTCP_RP2040W/src/AsyncTCP_RP2040W.h:84,
                 from .pio/libdeps/mks_tinybee/AsyncTCP_RP2040W/src/SyncClient.cpp:53:
/home/cedric/.platformio/packages/framework-arduinoespressif32/tools/sdk/include/lwip/lwipopts.h:326:0: warning: "TCP_MSS" redefined
 #define TCP_MSS                         CONFIG_TCP_MSS
 ^
In file included from .pio/libdeps/mks_tinybee/AsyncTCP_RP2040W/src/SyncClient.h:60:0,
                 from .pio/libdeps/mks_tinybee/AsyncTCP_RP2040W/src/SyncClient.cpp:52:
.pio/libdeps/mks_tinybee/AsyncTCP_RP2040W/src/async_config.h:35:0: note: this is the location of the previous definition
   #define TCP_MSS       MBED_CONF_LWIP_TCP_MSS        //(1460)
 ^
cc1plus: warning: unrecognized command line option '-Wno-register'
*** [.pio/build/mks_tinybee/lib19b/AsyncTCP_RP2040W/AsyncPrinter.cpp.o] Error 1
.pio/libdeps/mks_tinybee/AsyncTCP_RP2040W/src/AsyncTCP_RP2040W.cpp: In member function 'bool AsyncClient::connect(IPAddress, uint16_t)':
.pio/libdeps/mks_tinybee/AsyncTCP_RP2040W/src/AsyncTCP_RP2040W.cpp:331:8: error: 'ip_addr_t {aka struct ip_addr}' has no member named 'addr'
   addr.addr = ip;
        ^
.pio/libdeps/mks_tinybee/AsyncTCP_RP2040W/src/AsyncTCP_RP2040W.cpp: In member function 'bool AsyncClient::connect(const char*, uint16_t)':
.pio/libdeps/mks_tinybee/AsyncTCP_RP2040W/src/AsyncTCP_RP2040W.cpp:390:42: error: 'ip_addr_t {aka struct ip_addr}' has no member named 'addr'
     returnValue = connect(IPAddress(addr.addr), port);
                                          ^
In file included from .pio/libdeps/mks_tinybee/AsyncTCP_RP2040W/src/AsyncTCP_RP2040W.h:109:0,
                 from .pio/libdeps/mks_tinybee/AsyncTCP_RP2040W/src/AsyncTCP_RP2040W.cpp:104:
.pio/libdeps/mks_tinybee/AsyncTCP_RP2040W/src/AsyncTCP_RP2040W.cpp:393:73: error: 'ip_addr_t {aka struct ip_addr}' has no member named 'addr'
     ATCP_LOGDEBUG3("connect: dns_gethostbyname => IP =", IPAddress(addr.addr), ", returnValue = ", returnValue ? "TRUE" : "FALSE");
                                                                         ^
.pio/libdeps/mks_tinybee/AsyncTCP_RP2040W/src/AsyncTCP_RP2040W_Debug.h:87:128: note: in definition of macro 'ATCP_LOGDEBUG3'
 #define ATCP_LOGDEBUG3(x,y,z,w)  if(_ASYNCTCP_RP2040W_LOGLEVEL_>3) { ATCP_PRINT_MARK; ATCP_PRINT(x); ATCP_PRINT_SP; ATCP_PRINT(y); ATCP_PRINT_SP; ATCP_PRINT(z); ATCP_PRINT_SP; ATCP_PRINTLN(w); }
                                                                                                                                ^
.pio/libdeps/mks_tinybee/AsyncTCP_RP2040W/src/AsyncTCP_RP2040W.cpp: In member function 'bool AsyncClient::operator==(const AsyncClient&)':
.pio/libdeps/mks_tinybee/AsyncTCP_RP2040W/src/AsyncTCP_RP2040W.cpp:468:66: error: 'ip_addr_t {aka struct ip_addr}' has no member named 'addr'
   return (_pcb != NULL && other._pcb != NULL && (_pcb->remote_ip.addr == other._pcb->remote_ip.addr) &&
                                                                  ^
compilation terminated due to -fmax-errors=5.
*** [.pio/build/mks_tinybee/lib19b/AsyncTCP_RP2040W/AsyncTCP_RP2040W.cpp.o] Error 1
.pio/libdeps/mks_tinybee/AsyncTCP_RP2040W/src/async_config.h:35:25: error: 'MBED_CONF_LWIP_TCP_MSS' was not declared in this scope
   #define TCP_MSS       MBED_CONF_LWIP_TCP_MSS        //(1460)
                         ^
.pio/libdeps/mks_tinybee/AsyncTCP_RP2040W/src/SyncClient.h:86:34: note: in expansion of macro 'TCP_MSS'
     SyncClient(size_t txBufLen = TCP_MSS);
                                  ^
.pio/libdeps/mks_tinybee/AsyncTCP_RP2040W/src/async_config.h:35:25: error: 'MBED_CONF_LWIP_TCP_MSS' was not declared in this scope
   #define TCP_MSS       MBED_CONF_LWIP_TCP_MSS        //(1460)
                         ^
.pio/libdeps/mks_tinybee/AsyncTCP_RP2040W/src/SyncClient.h:87:55: note: in expansion of macro 'TCP_MSS'
     SyncClient(AsyncClient *client, size_t txBufLen = TCP_MSS);
                                                       ^
cc1plus: warning: unrecognized command line option '-Wno-register'
*** [.pio/build/mks_tinybee/lib19b/AsyncTCP_RP2040W/AsyncTCP_RP2040W_buffer.cpp.o] Error 1
cc1plus: warning: unrecognized command line option '-Wno-register'
*** [.pio/build/mks_tinybee/lib19b/AsyncTCP_RP2040W/SyncClient.cpp.o] Error 1
======================================================== [FAILED] Took 35.10 seconds ========================================================

Environment    Status    Duration
-------------  --------  ------------
mks_tinybee    FAILED    00:00:35.096
=================================================== 1 failed, 0 succeeded in 00:00:35.096 =================================================== ```

crocsg, 2025-03-26:
Alors ce qui m'inquiète c'est que je vois des erreurs qui concernent LWIP sur le RP2040 et je ne vois pas trop le lien avec la tinybee. Je  recharge le projet pour pouvoir le compiler et faire un diagnostique

crocsg, 2025-03-26:
Je viens de le recompiler avec VS code + platform IO et le plugin autobuild marlin
marlin2 correspond à la branche BrailleRAP à jour
dans le repertoire marlin, j'ai remplacé les fichiers Configuration.h et Configuration_adv.h par les fichiers correspondants du repertoire mks_tinybee de https://github.com/braillerap/MarlinBraille2Configuration

la ca compile sans probleme :
```
Linking .pio\build\mks_tinybee\firmware.elf
Building .pio\build\mks_tinybee\firmware.bin
Retrieving maximum program size .pio\build\mks_tinybee\firmware.elf
Checking size .pio\build\mks_tinybee\firmware.elf
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
crocsg, 2025-05-03:
Hum, there is some work on AsyncTCP with regular update that break compatibility. I will go back to LTS branch to fix it

crocsg, 2025-06-03:
Hi @vmario89 actually we have some issue with network lib in dependencies, at this time i would recommend a MKS GEN-L

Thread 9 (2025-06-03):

bom.rst does not list infos about the used type and amout of limit switches and spare parts

vmario89, 2025-06-03:
https://github.com/braillerap/BrailleRap/blob/master/docs/bom.rst is missing some more details about the required parts for going to shop. For BraillerapXL i extracted and summed up from building manual:

```
1  | 18mm spacer
2  | M2.5 nuts
2  | M2.5 NYL nut
4  | M2.5-14 screws
1  | M3 blind nut
5  | M3 nut
63 | M3 NYL nut
3  | M3 tap
5  | M3 washer
50 | M3 wide washer
1  | M3-12 grub screw with shaped tip (see Preparation of the Braille stylus)
6  | M3-12 screw
8  | M3-12 spacer
34 | M3-14 screw
1  | M3-16 dog point grub screw
10 | M3-16 screw
16 | M3-20 screw
9  | M3-25 screw
1  | M3-30 grub screw
13 | M3-6 grub screw
26 | M3-8 screw
8  | M5 NYL nut
8  | M5 washer
4  | M5-18 screw
4  | M5-25 screw
1  | Whetstone
2  | wired limit switch (see wiring of the limit switches)
```

i will try to add a commit while we build the machines in july, together with Hugues :-)

crocsg, 2025-06-03:
I see some issue (maybe in build manual), the
Braille stylus should be M3-16 dog point grub screw
all m2.5 nuts are nyl

we need a tool to automate list update

Closed 2025-06-15.

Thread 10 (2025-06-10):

List compatible types of limit switches

vmario89, 2025-06-10:
Hi,

for sourcing the parts it's helpful to have some compatible limit switch models in the BOM. I accidently ordered the wrong in terms of hole distance for now (the left one's in the photo):

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

i measured the X endstop STL file now to get a distance of 10 mm.

compatible model would be for example:
- CQC KW4-3Z-3 (https://www.ebay.de/itm/185242575152)

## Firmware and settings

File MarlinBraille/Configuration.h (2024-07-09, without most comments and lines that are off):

#define CONFIGURATION_H
#define CONFIGURATION_H_VERSION 010107
#define STRING_CONFIG_H_AUTHOR "BrailleRap marlin" // Who made the changes.
#define SHOW_BOOTSCREEN
#define STRING_SPLASH_LINE1 SHORT_BUILD_VERSION // will be shown during bootup in line 1
#define STRING_SPLASH_LINE2 WEBSITE_URL         // will be shown during bootup in line 2
#define SERIAL_PORT 0
#define BAUDRATE 250000
  #define MOTHERBOARD BOARD_RAMPS_14_SF
#define CUSTOM_MACHINE_NAME "Braille RAP"
#define SPINDLE_LASER_ENABLE
#define SPINDLE_LASER_ENABLE_PIN  RAMPS_D8_PIN      // !!! sortie BED MOSFET
#define SPINDLE_LASER_PWM_PIN     RAMPS_D10_PIN     // !!! sortie E0 MOSFET
#define SPINDLE_DIR_PIN           5                 // pin servo
#define BRAILLERAP_ELECTROMAGNET_DELAY	50
#define BRAILLERAP_AUTODISABL_MAGNET	1
#define PAPER_LOADING_HOME_Y 1 // homing Y load paper, you mut use YMIN endstop
#define EXTRUDERS 1
#define DEFAULT_NOMINAL_FILAMENT_DIA 3.0
#define POWER_SUPPLY 0
#define TEMP_SENSOR_0 1
#define TEMP_SENSOR_1 0
#define TEMP_SENSOR_2 0
#define TEMP_SENSOR_3 0
#define TEMP_SENSOR_4 0
#define TEMP_SENSOR_BED 0
#define DUMMY_THERMISTOR_998_VALUE 25
#define DUMMY_THERMISTOR_999_VALUE 100
#define MAX_REDUNDANT_TEMP_SENSOR_DIFF 10
#define TEMP_RESIDENCY_TIME 10  // (seconds)
#define TEMP_HYSTERESIS 3       // (degC) range of +/- temperatures considered "close" to the target one
#define TEMP_WINDOW     1       // (degC) Window around target to start the residency timer x degC early.
#define TEMP_BED_RESIDENCY_TIME 10  // (seconds)
#define TEMP_BED_HYSTERESIS 3       // (degC) range of +/- temperatures considered "close" to the target one
#define TEMP_BED_WINDOW     1       // (degC) Window around target to start the residency timer x degC early.
#define HEATER_0_MINTEMP 5
#define HEATER_1_MINTEMP 5
#define HEATER_2_MINTEMP 5
#define HEATER_3_MINTEMP 5
#define HEATER_4_MINTEMP 5
#define BED_MINTEMP 5
#define HEATER_0_MAXTEMP 275
#define HEATER_1_MAXTEMP 275
#define HEATER_2_MAXTEMP 275
#define HEATER_3_MAXTEMP 275
#define HEATER_4_MAXTEMP 275
#define BED_MAXTEMP 150
#define PIDTEMP
#define BANG_MAX 255     // Limits current to nozzle while in bang-bang mode; 255=full current
#define PID_MAX BANG_MAX // Limits current to nozzle while PID is active (see PID_FUNCTIONAL_RANGE below); 255=full current
#define PID_K1 0.95      // Smoothing factor within the PID
  #define PID_FUNCTIONAL_RANGE 10 // If the temperature difference between the target temperature and the actual temperature
  #define  DEFAULT_Kp 22.2
  #define  DEFAULT_Ki 1.08
  #define  DEFAULT_Kd 114
#define MAX_BED_POWER 255 // limits duty cycle to bed; 255=full current
#define PREVENT_COLD_EXTRUSION
#define EXTRUDE_MINTEMP 170
#define PREVENT_LENGTHY_EXTRUDE
#define EXTRUDE_MAXLENGTH 200
#define THERMAL_PROTECTION_HOTENDS // Enable thermal protection for all extruders
#define THERMAL_PROTECTION_BED     // Enable thermal protection for the heated bed
#define USE_XMIN_PLUG
#define USE_YMIN_PLUG
#define USE_ZMIN_PLUG
#define ENDSTOPPULLUPS // Comment this out (using // at the start of the line) to disable the endstop pullup resistors
#define X_MIN_ENDSTOP_INVERTING false // set to true to invert the logic of the endstop.
#define Y_MIN_ENDSTOP_INVERTING false // set to true to invert the logic of the endstop.
#define Z_MIN_ENDSTOP_INVERTING false // set to true to invert the logic of the endstop.
#define X_MAX_ENDSTOP_INVERTING false // set to true to invert the logic of the endstop.
#define Y_MAX_ENDSTOP_INVERTING false // set to true to invert the logic of the endstop.
#define Z_MAX_ENDSTOP_INVERTING false // set to true to invert the logic of the endstop.
#define Z_MIN_PROBE_ENDSTOP_INVERTING false // set to true to invert the logic of the probe.
#define DEFAULT_AXIS_STEPS_PER_UNIT   { 80 * 2, 87, 4000, 500 } // pololu 32 microstep with big roll
#define DEFAULT_MAX_FEEDRATE          { 300, 300, 5, 25 }
#define DEFAULT_MAX_ACCELERATION      { 3000, 1500, 100, 10000 }
#define DEFAULT_ACCELERATION          3000    // X, Y, Z and E acceleration for printing moves
#define DEFAULT_RETRACT_ACCELERATION  1500    // E acceleration for retracts
#define DEFAULT_TRAVEL_ACCELERATION   3000    // X, Y, Z acceleration for travel (non printing) moves
#define DEFAULT_XJERK                 5.0
#define DEFAULT_YJERK                 5.0
#define DEFAULT_ZJERK                  0.3
#define DEFAULT_EJERK                  5.0
#define Z_MIN_PROBE_USES_Z_MIN_ENDSTOP_PIN
#define X_PROBE_OFFSET_FROM_EXTRUDER 10  // X offset: -left  +right  [of the nozzle]
#define Y_PROBE_OFFSET_FROM_EXTRUDER 10  // Y offset: -front +behind [the nozzle]
#define Z_PROBE_OFFSET_FROM_EXTRUDER 0   // Z offset: -below +above  [the nozzle]
#define XY_PROBE_SPEED 8000
#define Z_PROBE_SPEED_FAST HOMING_FEEDRATE_Z
#define Z_PROBE_SPEED_SLOW (Z_PROBE_SPEED_FAST / 2)
#define MULTIPLE_PROBING 2
#define Z_CLEARANCE_DEPLOY_PROBE   10 // Z Clearance for Deploy/Stow
#define Z_CLEARANCE_BETWEEN_PROBES  5 // Z Clearance between probe points
#define Z_PROBE_OFFSET_RANGE_MIN -20
#define Z_PROBE_OFFSET_RANGE_MAX 20
#define X_ENABLE_ON 0
#define Y_ENABLE_ON 0
#define Z_ENABLE_ON 0
#define E_ENABLE_ON 0 // For all extruders
#define DISABLE_X false
#define DISABLE_Y false
#define DISABLE_Z false
#define DISABLE_E false // For all extruders
#define DISABLE_INACTIVE_EXTRUDER true // Keep only the active extruder enabled.
#define INVERT_X_DIR false
#define INVERT_Y_DIR false
#define INVERT_Z_DIR false
#define INVERT_E0_DIR false
#define INVERT_E1_DIR false
#define INVERT_E2_DIR false
#define INVERT_E3_DIR false
#define INVERT_E4_DIR false
#define X_HOME_DIR -1
#define Y_HOME_DIR 1
#define Z_HOME_DIR -1
#define X_BED_SIZE 310
#define Y_BED_SIZE 600
#define X_MIN_POS 0
#define Y_MIN_POS 0
#define Z_MIN_POS 0
#define X_MAX_POS X_BED_SIZE
#define Y_MAX_POS Y_BED_SIZE
#define Z_MAX_POS 200
#define MIN_SOFTWARE_ENDSTOPS
  #define MIN_SOFTWARE_ENDSTOP_X
  #define MIN_SOFTWARE_ENDSTOP_Y
  #define MIN_SOFTWARE_ENDSTOP_Z
#define MAX_SOFTWARE_ENDSTOPS
  #define MAX_SOFTWARE_ENDSTOP_X
  #define MAX_SOFTWARE_ENDSTOP_Y
  #define MAX_SOFTWARE_ENDSTOP_Z
#define MANUAL_Y_HOME_POS -20
#define Z_SAFE_HOMING
  #define Z_SAFE_HOMING_X_POINT ((X_BED_SIZE) / 2)    // X point for Z homing when homing all axes (G28).
  #define Z_SAFE_HOMING_Y_POINT ((Y_BED_SIZE) / 2)    // Y point for Z homing when homing all axes (G28).
#define HOMING_FEEDRATE_XY (20*60*2)
#define HOMING_FEEDRATE_Z  (4*60)
#define EEPROM_SETTINGS // Enable for M500 and M501 commands
#define EEPROM_CHITCHAT   // Give feedback on EEPROM commands. Disable to save PROGMEM.
#define HOST_KEEPALIVE_FEATURE        // Disable this if your host doesn't like keepalive messages
#define DEFAULT_KEEPALIVE_INTERVAL 2  // Number of seconds between "busy" messages. Set with M113.
#define BUSY_WHILE_HEATING            // Some hosts require "busy" messages even during heating
#define PREHEAT_1_TEMP_HOTEND 180
#define PREHEAT_1_TEMP_BED     70
#define PREHEAT_1_FAN_SPEED     0 // Value from 0 to 255
#define PREHEAT_2_TEMP_HOTEND 240
#define PREHEAT_2_TEMP_BED    110
#define PREHEAT_2_FAN_SPEED     0 // Value from 0 to 255
#define PRINTJOB_TIMER_AUTOSTART
#define LCD_LANGUAGE fr
#define DISPLAY_CHARSET_HD44780 JAPANESE
#define SOFT_PWM_SCALE 0
#define SERVO_DELAY { 300 }

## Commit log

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2022-06-15 work in progress
    [BOTTOM_trolley_rework.stl, BrailleRAP V5 600x400 planche1.dxf, BrailleRAP V5 600x400 planche1_r14.dxf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]
2022-06-27 V6 RC
    [3D printed parts excel board.xlsx, ELECTRO_MAGNET_guide.stl, PAPERGUIDE_left.stl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]
2022-06-29 v6 rc1
    [BOTTOM_trolley.stl, BOTTOM_trolley_rework.stl, BrailleRAP V5 600x400 planche1.dxf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]
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2022-06-30 Update doc - add download link for MKS USB drivers
    [cle_hex_5-5.stl]
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2022-07-02 Update paper support assembly doc
    [rizlan_profile1.dxf, rizlan_profile2.dxf]
2022-07-11 update M3 S1 to disable electromagnet after small delay
    [Configuration.h]
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2022-11-30 update electromagnet housing. Stronger design, more positionning option for the electromagnet
    [ELECTRO_MAGNET_housing.stl]
2022-12-31 update doc
    [STP - 4445589 - TPS M-3X0.5-M - Basic-mm.f3d]
2022-12-31 update doc clipboard
    [FEMALE_shape2.stl]
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2023-01-01 update doc electronique
    [rizlan_profile1.dxf, rizlan_profile2.dxf]
2023-01-01 adjust ENDSTOP_Y_support
    [ENDSTOP_Y_support.stl]
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2023-01-02 test ELECTRO_MAGNET_guide tolerance
    [ELECTRO_MAGNET_guide.stl, ELECTRO_MAGNET_guide_fit.stl]
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2023-04-10 update motor support
    [BrailleRAP V6-5 600x400 planche1.dxf, BrailleRAP V6-5 600x400 planche2.dxf, BrailleRAP V6-5 600x400 plate1.dxf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]
2023-05-03 update motor support, trolley marking
    [BOTTOM_trolley_rework.stl, ELECTRO_MAGNET_guide_fit_5.8.stl, ELECTRO_MAGNET_guide_fit_5.9.stl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]
2023-05-03 Update clipboard
    [clipboard2.stl]
2023-05-05 update doc support motor X
    [door_lock.stl]
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2023-05-05 update motor Y support
    [YMOTOR_support2_200_1.stl, YMOTOR_support2_200_2.stl]
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2023-05-16 update doc img
    [clip_2.stl]
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2023-05-19 stl cleaning
    [3D printed parts excel board.xlsx, BOTTOM_trolley_rework.stl, XMOTOR_support.stl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]
2023-10-08 Update readme and lasercut files
    [BrailleRAP V6 600x400 planche1.dxf, BrailleRAP V6 600x400 planche2.dxf, BrailleRAP V6-5 600x400 plate1.dxf]
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2024-03-05 update lasercut file for better door closing system with PMMA
    [BrailleRAP V6-5 600x400 planche1.dxf, BrailleRAP V6-5 600x400 planche2.dxf, Braillerap_v6-5-1-600x400-planche2.dxf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]
2024-03-05 update 3d printed parts board
    [3D printed parts excel board.xlsx]
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2024-05-25 update default speed and accel
    [Configuration.h]
2024-05-25 stronger part and less tolerance
    [3D printed parts excel board.ods, BOTTOM_AXIS_right2.stl, TOP_AXIS_right2.stl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]
2024-06-09 Paper guide for BrailleRAP XL
    [paper_guide_left_A3.stl, paper_guide_right_A3.stl]
2024-06-09 cable path for BrailleRAP XL
    [passecable.stl]
2024-06-09 upgrade printed parts
    [BOTTOM_AXIS_left.stl, BOTTOM_AXIS_right.stl, ENDSTOP_Y_lever.stl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]
2024-06-09 update printed parts
    [DRIVEN_PULLEY_housing.stl, FEMALE_shape.stl, FEMALE_shape2.stl]
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2024-06-28 update paper guide for xl
    [paper_guide_left_XL.stl, paper_guide_right_XL.stl]
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2024-07-03 update solenoid guides
    [ELECTRO_MAGNET_guide_fit_5.7.stl, ELECTRO_MAGNET_guide_fit_5.8.stl, ELECTRO_MAGNET_guide_fit_5.9.stl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]
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2024-07-09 update bed size for XL
    [Configuration.h]
2024-10-02 test new lever
    [ENDSTOP_Y_lever_weight2.stl]
2024-12-14 new design for easy printing
    [XMOTOR_support3_1_2.stl]
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2024-12-16 add a tiny chamfer for better printing
    [CLIPBOARD2_WHEEL.stl]
2025-01-06 better tolerance and conic nuts dimension
    [cle_hex_5-5.stl]
2025-01-06 improve 3d print result
    [XMOTOR_support3_1.stl, XMOTOR_support3_1_2.stl]
2025-01-06 test new roll joint for better 3d print
    [ROLL_JOINT2_test.stl]
2025-01-25 update 3d parts to print
    [3D printed parts excel board.ods]
2025-03-11 better 3d print quality
    [YMOTOR_support2_200.stl, YMOTOR_support2_200_1.stl]
2025-04-17 update cad
    [ROLL_JOINT2.stl, ROLL_JOINT2_test.stl]
2025-04-17 update paper support
    [Braillerap_v6-5-1-600x400-planche2.dxf, Braillerap_v6-5-1_600x400-planche1.dxf]
2025-05-03 Translated using Weblate (English)
    Currently translated at 100.0% (346 of 346 strings)
    Translation: BrailleRAP Building manual/manual_assemblage
    Translate-URL: https://translate.codeberg.org/projects/braillerap-building-manual/manual_assemblage/en/
2025-05-04 Translated using Weblate (English)
    Currently translated at 100.0% (3 of 3 strings)
    Translation: BrailleRAP Building manual/braillerap_glossary
    Translate-URL: https://translate.codeberg.org/projects/braillerap-building-manual/braillerap_glossary/en/
2025-05-04 Translated using Weblate (English)
    Translation: BrailleRAP Building manual/manual_index
    Translate-URL: https://translate.codeberg.org/projects/braillerap-building-manual/manual_index/en/
    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
2025-05-04 Translated using Weblate (English)
    Currently translated at 100.0% (40 of 40 strings)
    Translation: BrailleRAP Building manual/manual_bom
    Translate-URL: https://translate.codeberg.org/projects/braillerap-building-manual/manual_bom/en/
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2025-07-07 add power plate for 10mm diameter power jack 2.5
    [power_plate_10mm.stl]
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2025-10-28 fix motor wiring in english manual
2025-10-29 update printed parts board. Improve 3d plastic parts for printability
    [3D printed parts board.ods, 3D printed parts excel board.ods, 3D printed parts excel board.xlsx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]
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2026-02-27 Upgrade tolerance
    [ENDSTOPX_support2.stl]
2026-06-03 Fix glued words and doubled URL in English documentation
    PO files concatenate adjacent quoted continuation strings with no
    whitespace inserted, so a trailing space must live inside the closing
    quote. Several msgstr entries were missing those spaces, producing
    glued output in the rendered HTML such as 'directoryhttps://...',
    'pasteto', and 'screenSelect'.
    Separately, docs/history.rst contained a doubled protocol
    (<https://https://github.com/.../AccessBrailleRAP>) which carried
    through msgid and msgstr in history.po and breaks the link in both
    language renderings.
    Fixes:
    * marlin.po - 3 fixes (controlWe; trailing spaces before the URL and
    before 'directly')
    * firstembossingpage.po - 5 trai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

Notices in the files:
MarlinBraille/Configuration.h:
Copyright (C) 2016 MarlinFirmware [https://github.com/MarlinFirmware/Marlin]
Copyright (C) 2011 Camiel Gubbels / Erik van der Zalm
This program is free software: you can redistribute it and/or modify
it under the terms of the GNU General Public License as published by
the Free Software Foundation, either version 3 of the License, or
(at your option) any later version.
